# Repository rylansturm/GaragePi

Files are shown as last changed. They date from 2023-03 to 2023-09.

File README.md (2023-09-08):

# GaragePi

#### UPDATE 9/7/2023

About a month ago I got the case printed and everything mounted in my garage.
The sensors are IR prox sensors that sit just above the door when closed, but
the PCB can work with anything that has a 3.3V, GND, and Sensor pin configuration.
The wiring is a CAT5 cable terminated with an aviation plug on the Pi side and
screw terminals on the sensor side.

I can access the Pi remotely via SSH. I am now working on setting up an MQTT 
(Mosquitto) broker on my home network. Then I'll work on setting up an API and
GUI on my public server so remote access is more user friendly.

## Specs

#### Basic Requirements

Non-destructive. The project must not remove anything from the current
garage door system. Wires can be added into and below the physical 
buttons that are on the garage wall now. Disconnection should be easy.

Open/Close. A relay can be used to make the connection that send the
signal to the garage openers. 

Scalable. The system should support my two garage doors, and
should ideally be scalable up or down easily. One door without useless
clutter in the UI, 3 doors just as simply.

Sensors. I should be able to read the current state of the garage.

#### MVP

A minimum viable project is one where I can control my garage door
via ssh when connected to WiFi. That just means Raspberry Pi, 
Relay board, and a local bash script. Let's go.

#### UPDATE 3/20/2023

Minimum viable project is in place. I can now open and close garage doors
by running the rust script with argument '1' or '2'. Only from local network.
No monitoring system in place

#### UPDATE 6/26/2023

A PCB has been designed that will sit on top of the Pi.
It has been ordered and should be in place in the next week or so.
Now on to designing the sensors.

#### PCB Design

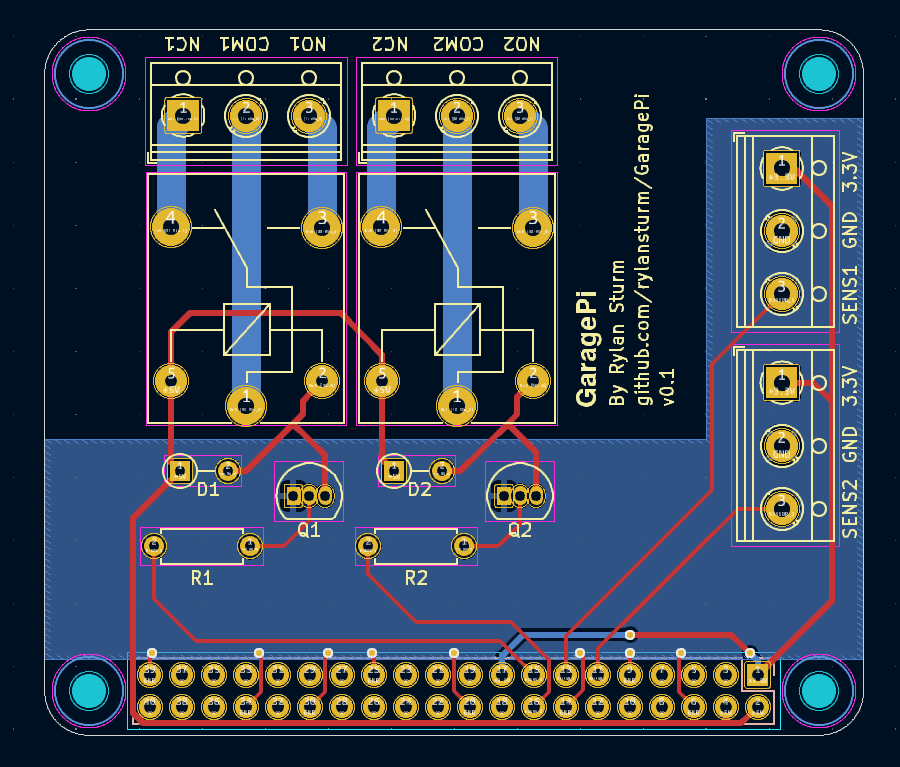
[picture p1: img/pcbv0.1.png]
PCB Design


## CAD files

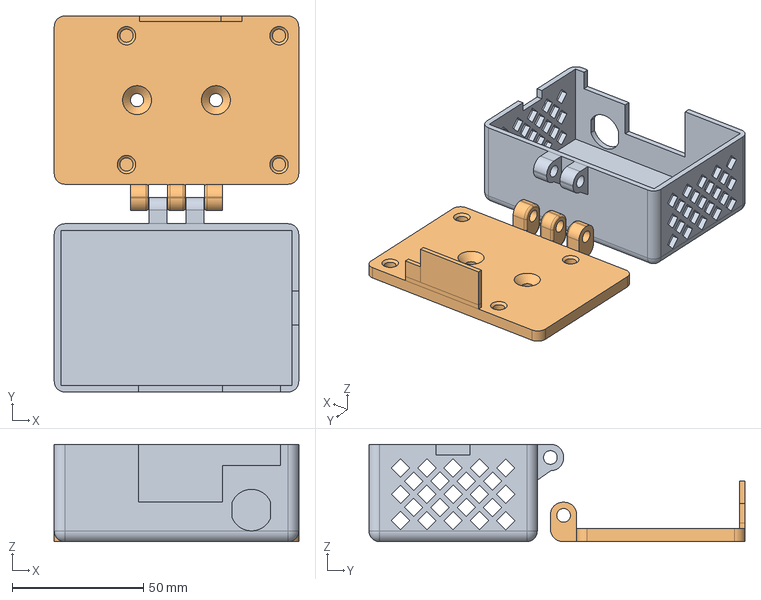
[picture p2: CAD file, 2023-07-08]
CAD/GaragePi_Housing.FCStd
93.0 x 143.0 x 37.0 mm

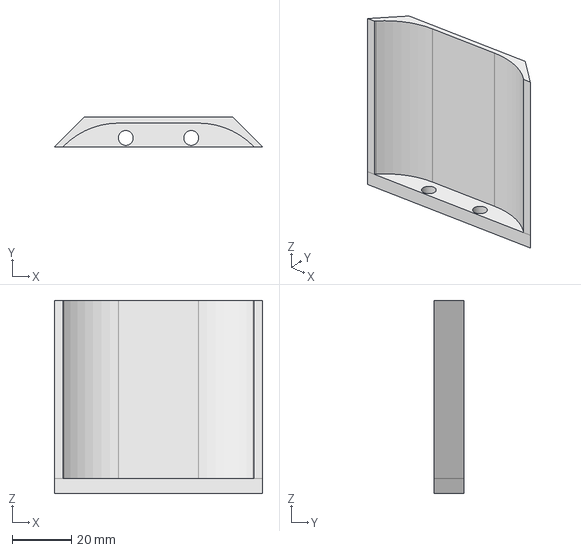
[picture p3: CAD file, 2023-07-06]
CAD/Door_Sensor_Reflector.FCStd
70.0 x 10.0 x 65.0 mm

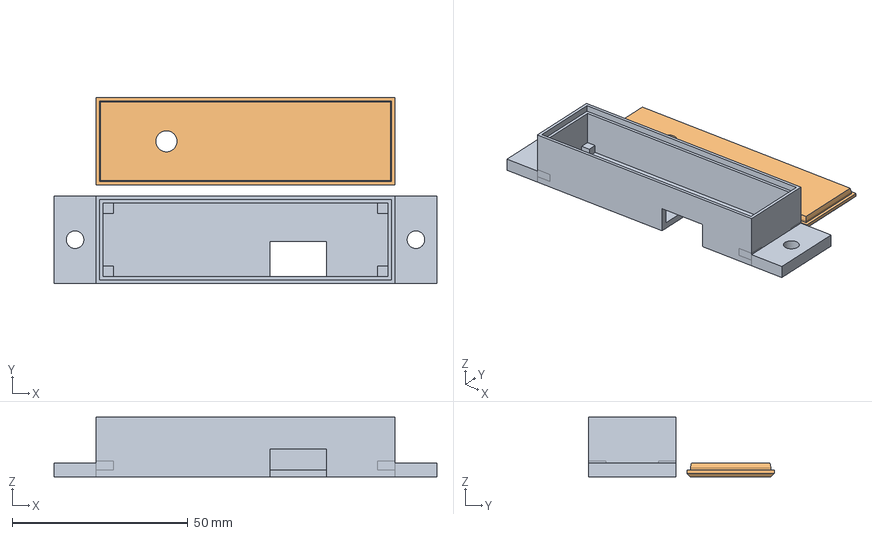
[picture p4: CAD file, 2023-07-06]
CAD/Sensor_Housing.FCStd
109.0 x 53.0 x 17.0 mm

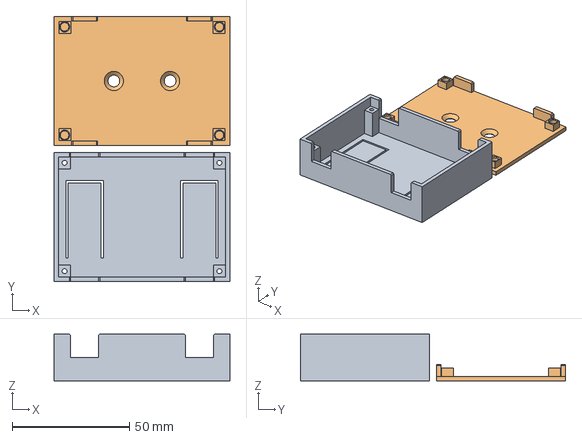
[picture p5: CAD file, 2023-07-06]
CAD/Button_Housing.FCStd
75.0 x 113.0 x 20.0 mm

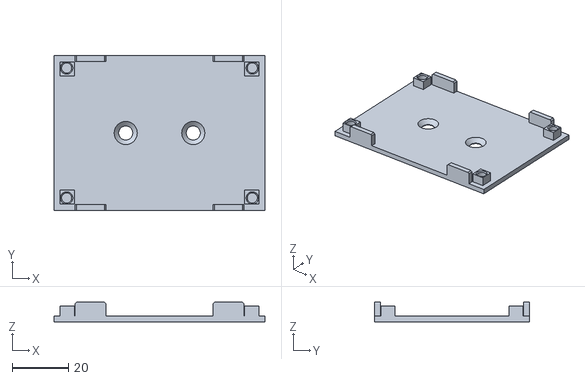
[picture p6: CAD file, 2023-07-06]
CAD/Button_Housing-Wall_Plate.stl
75.0 x 55.0 x 7.00

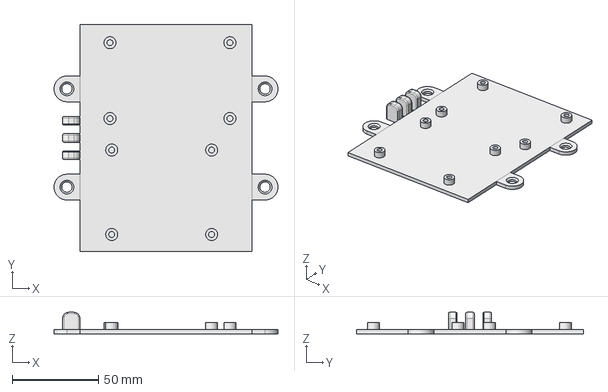
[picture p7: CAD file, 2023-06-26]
CAD/Bottom_Plate.FCStd
130.0 x 132.0 x 12.5 mm

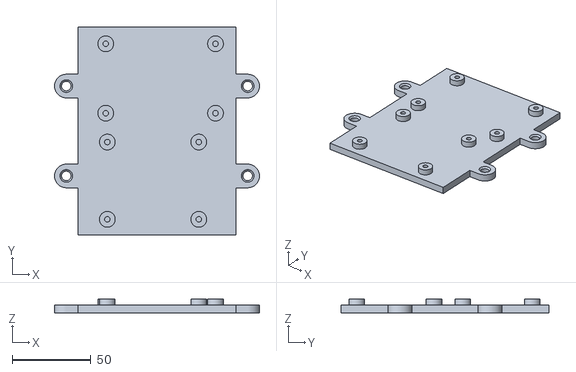
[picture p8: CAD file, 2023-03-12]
CAD/Bottom_Plate-Body.stl
130.0 x 132.0 x 9.00

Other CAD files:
CAD/Button_Housing.stl
CAD/Door_Sensor_Reflector.stl
CAD/GaragePi_Housing.stl
CAD/Sensor_Housing.stl

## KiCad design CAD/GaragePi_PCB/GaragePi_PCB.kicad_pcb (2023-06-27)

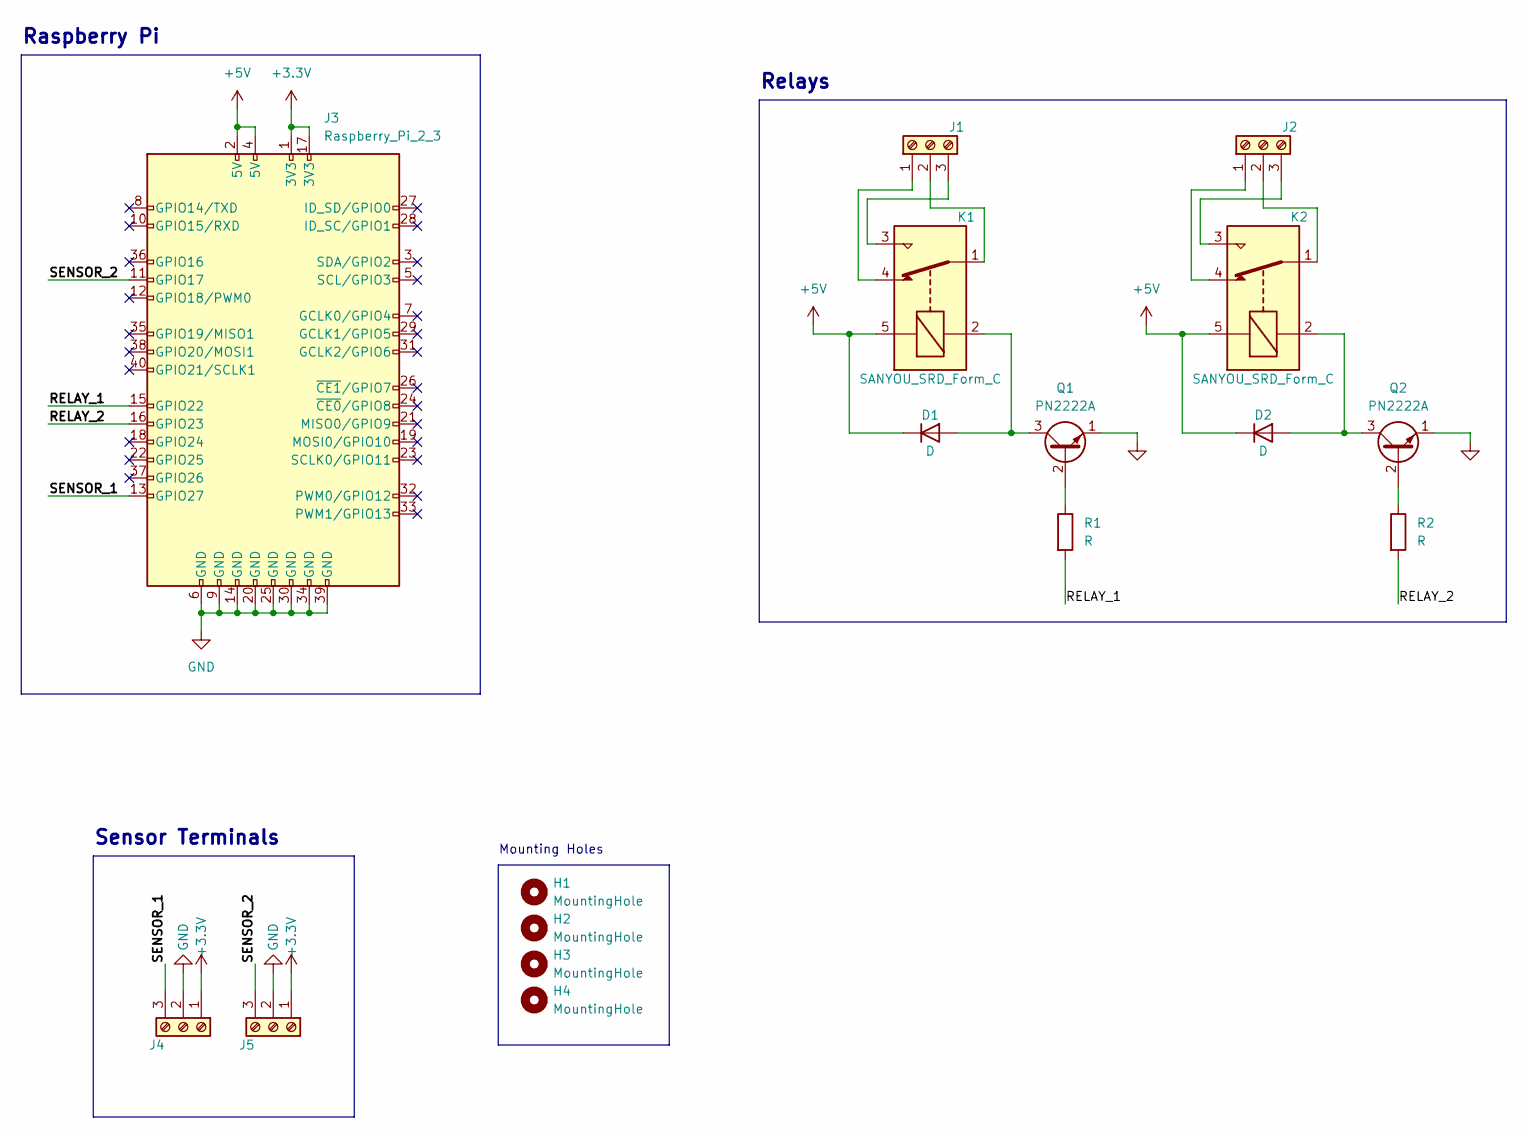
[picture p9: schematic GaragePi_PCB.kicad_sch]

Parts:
D1, D2: D; D_DO-35_SOD27_P3.81mm_Vertical_AnodeUp
H1, H2, H3, H4: MountingHole; MountingHole_2.7mm_M2.5
J1, J2, J4, J5: Screw_Terminal_01x03; TerminalBlock_RND_205-00013_1x03_P5.00mm_Horizontal
J3: Raspberry_Pi_2_3; PinSocket_2x20_P2.54mm_Vertical
K1, K2: SANYOU_SRD_Form_C; Relay_SPDT_SANYOU_SRD_Series_Form_C
Q1, Q2: PN2222A; TO-92_Inline
R1, R2: R; R_Axial_DIN0207_L6.3mm_D2.5mm_P7.62mm_Horizontal

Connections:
+3.3V: J3.1 (3V3), J3.17 (3V3), J4.1, J5.1
+5V: D1.1 (K), D2.1 (K), J3.2 (5V), J3.4 (5V), K1.5, K2.5
/RELAY_1: J3.15 (GPIO22), R1.2
/RELAY_2: J3.16 (GPIO23), R2.2
/SENSOR_1: J3.13 (GPIO27), J4.3
/SENSOR_2: J3.11 (GPIO17), J5.3
GND: J3.6 (GND), J3.9 (GND), J3.14 (GND), J3.20 (GND), J3.25 (GND), J3.30 (GND), J3.34 (GND), J3.39 (GND), J4.2, J5.2, Q1.1 (E), Q2.1 (E)
unnamed: D1.2 (A), K1.2, Q1.3 (C)
unnamed: D2.2 (A), K2.2, Q2.3 (C)
unnamed: J1.1, K1.4
unnamed: J1.2, K1.1
unnamed: J1.3, K1.3
unnamed: J2.1, K2.4
unnamed: J2.2, K2.1
unnamed: J2.3, K2.3
unnamed: Q1.2 (B), R1.1
unnamed: Q2.2 (B), R2.1

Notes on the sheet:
Mounting Holes
Sensor Terminals
Raspberry Pi
Relays

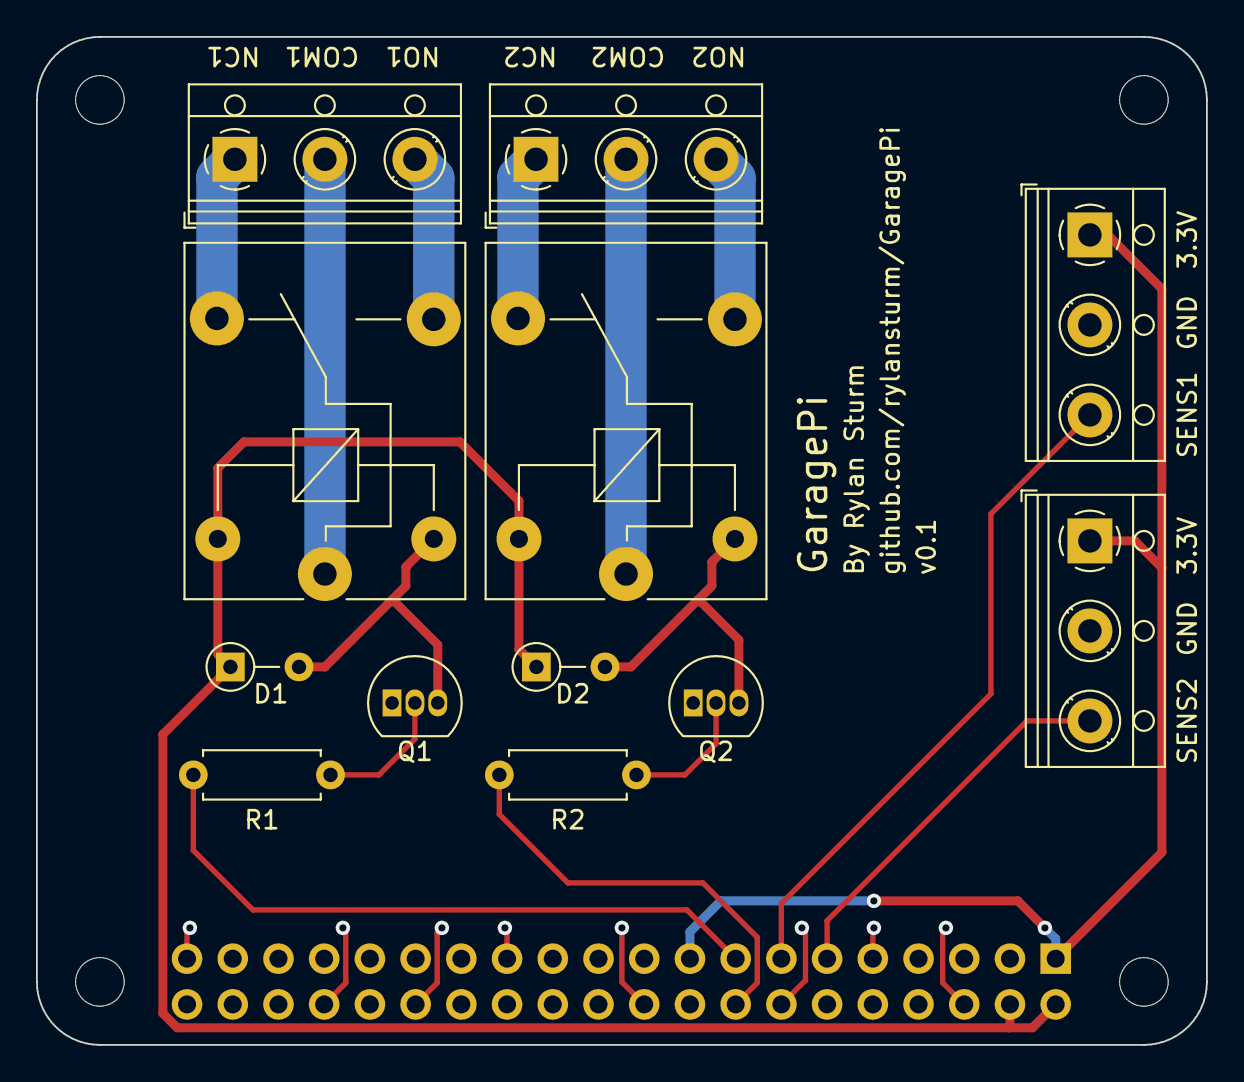
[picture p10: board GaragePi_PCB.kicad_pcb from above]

Board: 2 copper layers, 65.0 x 56.0 mm, 17 parts (1 on the bottom side), 17 nets.

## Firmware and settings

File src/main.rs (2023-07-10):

use rust_gpiozero::*;
use std::thread;
use std::time::Duration;
use std::env;

const DOOR1RELAY: u8 = 22;
const DOOR1SENSOR: u8 = 27;
const DOOR2RELAY: u8 = 23;
const DOOR2SENSOR: u8 = 17;

mod commands;

fn main() {
    let args: Vec<String> = env::args().collect();
    
    if check_args(&args) {
        let command = &args[1];
        let door = &args[2];

        match command.as_str() {
            "open" => open(door),
            "close" => close(door),
            "check" => check(door),
            _ => println!("invalid command \"{}\".", command.as_str()),
        }
    }
}

fn check_args(args: &Vec<String>) -> bool {
    if args.len() != 3 {
        println!("Command failed length constraint.\nCommand must be 2 arguments, ex. 'open 1'");
        return false;
    }
    if !commands::COMMANDS.contains(&args[1].as_str()) {
        println!("command failed first argument constraint.\nFirst argument must be 'open', 'close', or 'check'");
        return false;
    }
    if !commands::DOORS.contains(&args[2].as_str()) {
        println!("Command failed second argument constraint.\nSecond argument must be '1' or '2'");
        return false;
    }
    true
}

fn open(door: &String) {
    if !status(door) {
        println!("opening door {}", door);
        press(&door);
    } else {
        println!("door {} is already open", door);
    }
}

fn close(door: &String) {
    if status(door) {
        println!("closing door {}", door);
        press(&door);
    } else {
        println!("door {} is already closed", door);
    }
}

fn check(door: &String) {
    let status: String = match status(door) {
        false => String::from("closed"),
        true => String::from("open"),
    };
    println!("door {} is {}", door, status);
}

fn press(door: &String) {
    let doorpin: u8 = match door.as_str() {
        "1" => DOOR1RELAY,
        "2" => DOOR2RELAY,
        _ => 0,
    };
    let door = LED::new(doorpin);
    door.on();
    thread::sleep(Duration::from_millis(250));
    door.off();
}

fn status(door: &String) -> bool {
    let doorpin: u8 = match door.as_str() {
        "1" => DOOR1SENSOR,
        "2" => DOOR2SENSOR,
        _ => 0,
    };
    InputDevice::new(doorpin).value()
}

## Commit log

2023-02-06 Added pin functionality
2023-03-12 added v0.1 of the baseplate
    [Bottom_Plate-Body.stl, Bottom_Plate.FCStd]
2023-03-12 Fixed hole width on relay mount
    [Bottom_Plate-Body.stl, Bottom_Plate.FCStd]
2023-03-21 no longer using python for controlling relays
2023-06-26 added kicad files v0.1
    [Bottom_Plate.FCStd, GaragePi_PCB.kicad_pcb, GaragePi_PCB.kicad_sch]
2023-06-27 completed PCB schematics v0.1; Updated README with the project update
    [GaragePi_PCB-B_Cu.gbr, GaragePi_PCB-B_Mask.gbr, GaragePi_PCB-B_Paste.gbr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]
2023-06-27 Added img folder and pcbv0.1.png
2023-07-06 modeled buttons; Started housing for GaragePi
    [Button_Housing-Wall_Plate.stl, Button_Housing.FCStd, Button_Housing.stl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]
2023-07-06 first printable GaragePi housing
    [GaragePi_Housing.FCStd, GaragePi_Housing.stl]
2023-07-08 modified GaragePi_Housing to accomodate sd card and so hinge aligned
    [GaragePi_Housing.FCStd, GaragePi_Housing.stl]
2023-07-10 working Rust script. Needs validation and error handling
    [main.rs]
2023-07-10 added argument validation and error messages in Rust script
    [main.rs]
